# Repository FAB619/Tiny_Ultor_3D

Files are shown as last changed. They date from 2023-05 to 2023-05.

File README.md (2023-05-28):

<div align="center"><h1 style=align="center">Tiny ULTOR</h1></div>

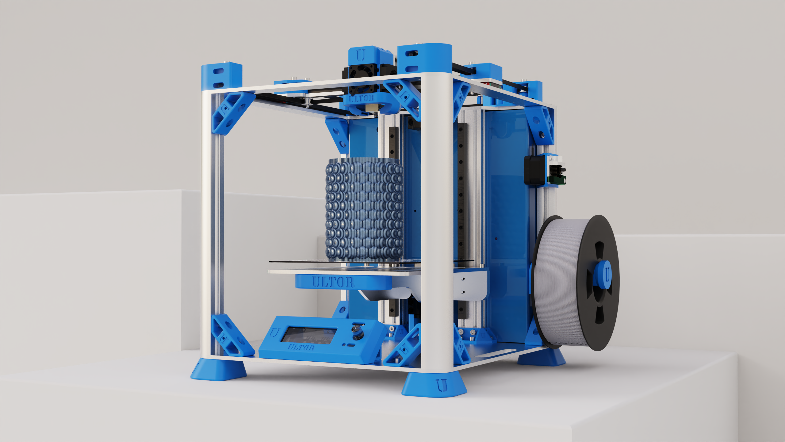
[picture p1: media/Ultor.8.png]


Introduction 
--
Welcome to the **TINY ULTOR** machine documentation.

**We are excited to share our open-source 3D printer project in collaboration with Inmachines Gmbh!!**

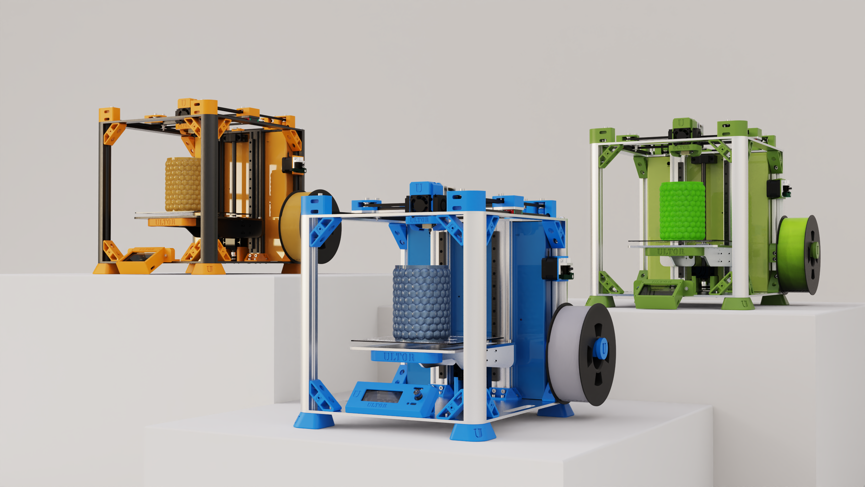
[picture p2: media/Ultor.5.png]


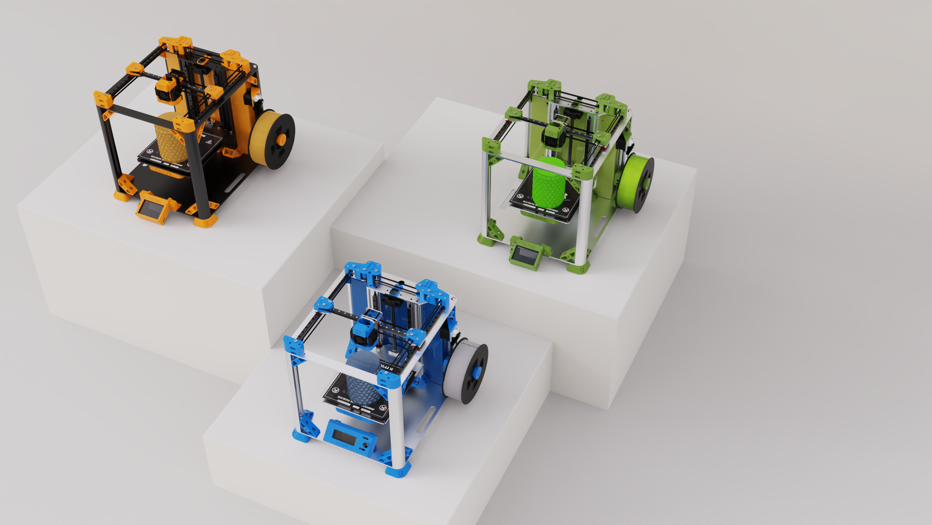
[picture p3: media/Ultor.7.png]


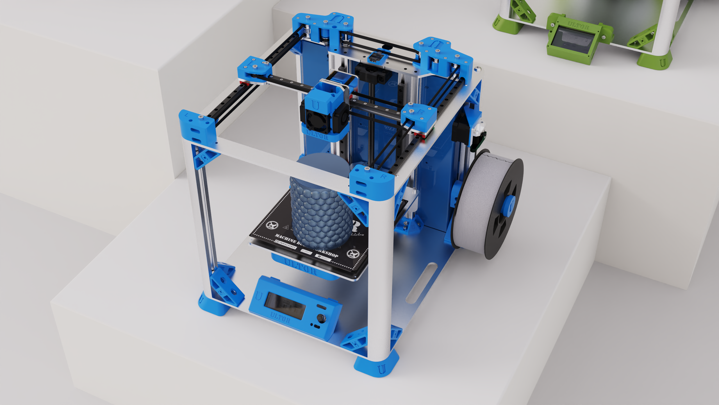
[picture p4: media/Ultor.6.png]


Specifications
--
- Build volume: 200x200x200mm
- Sturdy aluminium frame for stability and reduced vibration
- bed: aluminum with  non-sticking layer
- motion: COREXY system with GT2 6mm belt, Z axis: Sfu 1204 Ballscrew.
- guides: 9 & 12mm linear shaft, Hiwin MGN Series 9 & 12mm linear rails. MGN9 for XY axis an MGN12 for Z axis.
- motors: stepper motor NEMA 17
- drivers: trinamic TMC2208
- adjustable and heated printing bed
- Screens: Touchscreen HMI interface for easy operation / Reprap LCD 2004
- Pcb Board: **[Rumba3D-SPLink](https://github.com/FAB619/Rumba3D-SPLink)** board.

Electronics
----

Electronics design are one of the key features of FAB619 products. All products are 100% designed & made in tunisia. The electronics and boards are designed locally and fully functional with more addons.



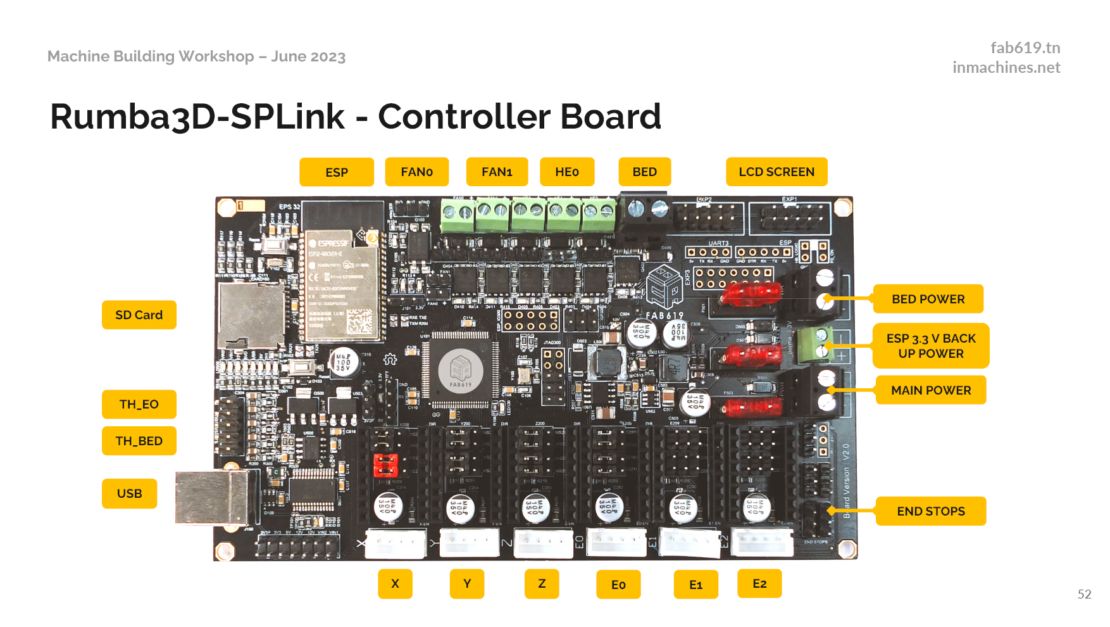
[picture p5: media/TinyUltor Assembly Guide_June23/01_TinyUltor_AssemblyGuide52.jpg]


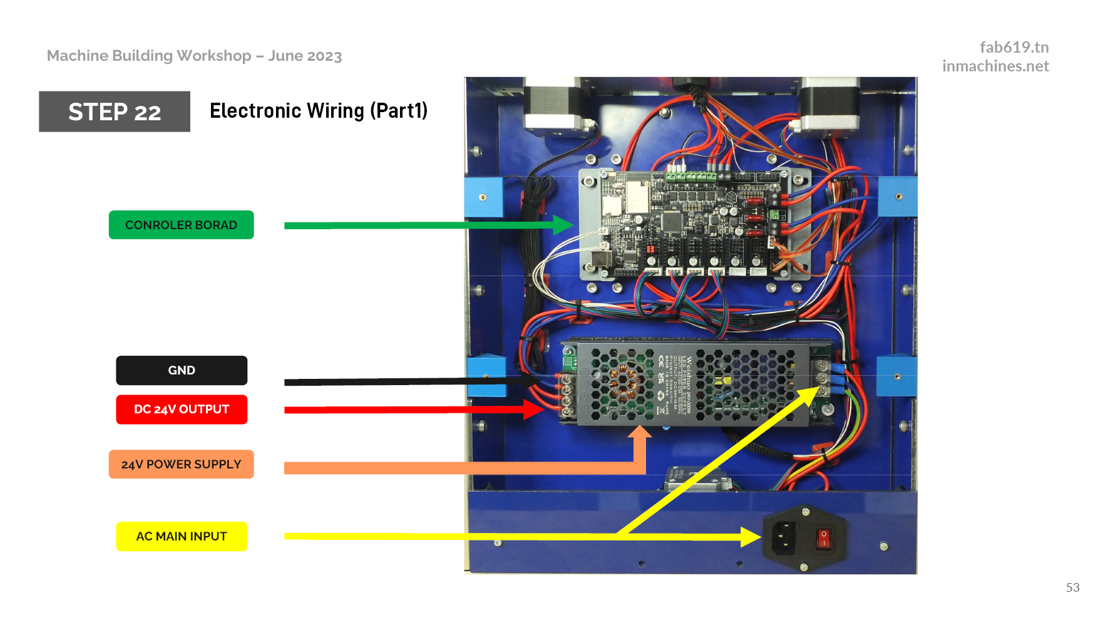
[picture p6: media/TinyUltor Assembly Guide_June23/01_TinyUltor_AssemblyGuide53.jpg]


Files 
--
 - **[CAD Files](https://github.com/FAB619/Tiny_Ultor_3D/tree/main/CAD)**
 - **[Fabrication Files](https://github.com/FAB619/Tiny_Ultor_3D/tree/main/Fabrication)**
- **[Assembly Book](https://github.com/FAB619/Tiny_Ultor_3D/wiki/Tiny-Ultor-3D-Assembly-Guide)**
- **[Firmware ](https://github.com/FAB619/Tiny_Ultor_3D/tree/main/Firmware/Marlin-2.0.9.6)**

3D printing Test 
--
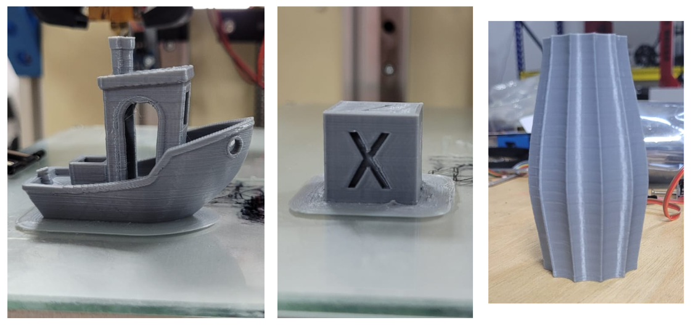
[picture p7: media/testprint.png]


Acknowledgements
--
The development of this machine is part of **Digital4Job Project** implemented by: 
* **[Helmut-Schmidt-Universität Universität der Bundeswehr](https://www.hsu-hh.de/en/)** Laboratorium Fertigungstechnik Holstenhofweg 85 22043 Hamburg
* **[OpenLab Hamburg](https://openlab-hamburg.de/startpage/)**
* **[GIZ](https://www.giz.de/en/worldwide/326.html)**

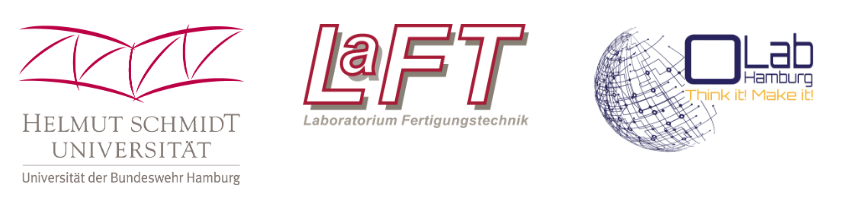
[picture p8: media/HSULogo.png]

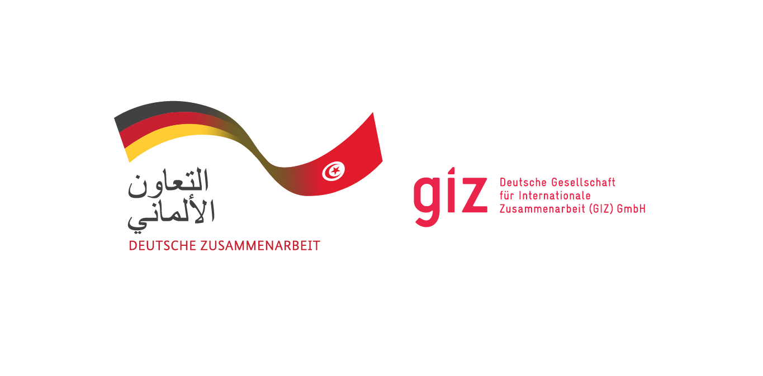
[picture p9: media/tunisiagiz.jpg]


In partnership with: 
* **[InMachines Ingrassia GmbH](https://www.inmachines.net/)**

* **[Fab619 On-Demand-Fabrication](https://fab619.tn/)**



License
--

Hardware design, CAD and PCB files, BOM, settings and other technical or design files are released under the following license:

- CERN Open Hardware Licence Version 2 Weakly Reciprocal - **[CERN-OHL-W](LICENSE_CERN_OHL_W_V2.txt)**

Assembly manual, pictures, videos, presentations, description text and other type of media are released under the following license:

- Creative-Commons-Attribution-ShareAlike 4.0 International - **[CC BY-SA 4.0](LICENSE_CC_BY_SA_4.0.txt)**

**License Owner **[InMachines Ingrassia GmbH](https://www.inmachines.net/)****

Author
--

**Tiny ULTOR** 3D Printer has been designed and built by **[Fab619 On-Demand-Fabrication](https://fab619.tn/)** & **[InMachines Ingrassia GmbH](https://www.inmachines.net/)**.



<br>

<b>FAB619 Design Team:</b>

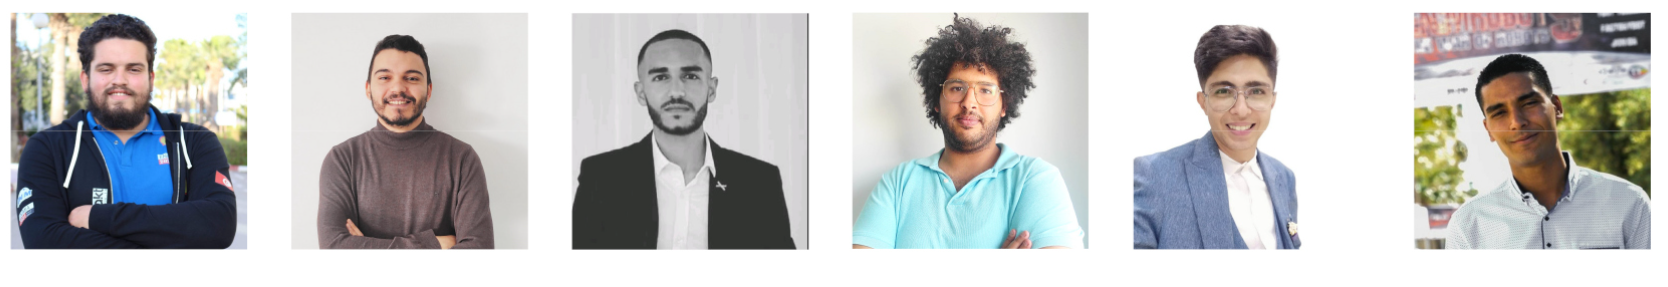
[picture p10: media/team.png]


<b> [Kais ALILA](http://fabacademy.org/2020/labs/kamplintfort/students/kais-alila/) | [Mhamed ALILA](https://www.behance.net/alilamhamed) | [Zomita Khayreddine](https://www.linkedin.com/in/zomita-khayreddine-916718217/) | [Ltifi Haythem](https://www.linkedin.com/in/haythemltifi/) | [Samer Jawadi](https://www.linkedin.com/in/samer-jawadi/) | [Ahmed Kaddour Belaid](https://www.linkedin.com/in/ahmed-kaddour-belaid-a6854418a/) </b>

Note
--
This documentation will be continuously improved as soon there are updates and/or improvements on the machine.

Disclaimer
--

This hardware/software is provided "as is", and you use the hardware/software at your own risk. Under no circumstances shall any author be liable for direct, indirect, special, incidental, or consequential damages resulting from the use, misuse, or inability to use this hardware/software, even if the authors have been advised of the possibility of such damages.

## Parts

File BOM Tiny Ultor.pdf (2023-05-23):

Category | ID | Item | Qte
| 1 | Nema 17 17HS4401 0.49NM | 4
| 2 | TMC2208 - Stepper Driver | 4
| 3 | Extruder Head CR8 1.75mm Nozzle 0.4mm 24V | 1
| 4 | Heat Bed MK2B | 1
| 5 | AC PSU Cable | 1
| 6 | PSU 24V 12,5A 300W | 1
| 7 | PCB Board Rumba Plus FAB619 | 1
| 8 | Turbo Cooling FAN 24V 40x40x10mm | 1
| 9 | Cooling FAN 12V 40x40x10mm | 1
| 10 | PI Zero WH | 1
| 11 | TFT screen RPI 3,5inch | 1
| 12 | LCD 2004 Reprap Screen | 1
| 13 | HDMI Cable | 1
| 14 | USB Tyope B cable | 1
| 15
| 16
| 17 | 2GT-20-6 T 5M Pulley Z=20 | 2
| 18 | 2GT-6 T=5mm Idler pulley 6mm | 14
| 19 | MGN9 300MM + MGN9H | 1
| 20 | MGN9 350MM + MGN9H | 2
| 21 | MGN2 300MM + MGN12H | 2
| 22 | Brass Spacer M3*30*6MM | 4
| 23 | Brass Spacer M3*10*6MM | 4
| 24 | SFU1204-300MM BallScrew | 1
| 25 | BK10 bearing | 1
| 26 | BF10 Bearing | 1
| 27 | MK8 Extruder 1.75MM right | 1
| 28 | 2GT-20-6 T=8MM Pulley Z= 60 | 1
| 29 | 2GT-60-6 T=5MM Pulley Z= 60 for 6MM Tinming belt | 1
| 30 | Aluminium Extrusion Rounded 30x30 R8 L2000MM | 1
| 31 | Machine Footer D=40mm M8 | 4
| 32

### Mecanichal Parts

### Electronics

Raw Material | 33
| 34 | PLA 1,75 1kg | 2
| 35 | Plexiglass Acrilyc 4mm Transparen 500x500mm | 1
| 36 | Aluminium Composites 3mm Blue 500x500mm | 1
| 37
| 38 | DIN912 M3x8 | 150
| 39 | DIN912 M3x12 | 28
| 40 | DIN912 M3x14 | 4
| 41 | DIN912 M3x16 | 23
| 42 | DIN912 M3x25 | 4
| 43 | DIN912 M3x30 | 4
| 44 | DIN912 M4x10 | 10
| 45 | DIN912 M5x10 | 62
| 46 | DIN912 M5x16 | 6
| 47 | DIN912 M5x25 | 4
| 48 | DIN912 M5x30 | 2
| 49 | DIN912 M5x40 | 13
| 50 | ISO7380 M6x10 | 8
| 51 | ISO7380 M8x16 | 4
| 52 | T-Nut M3 R6 2020 | 24
| 53 | T-Nut M5 R8 3030 | 26
| 54 | T-Nut M5 R6 2020 | 16
| 55 | T-Nut M4 R8 3030 | 2
| 56 | M3 Nut | 16
| 57 | M5 Nut | 2

### Fastners

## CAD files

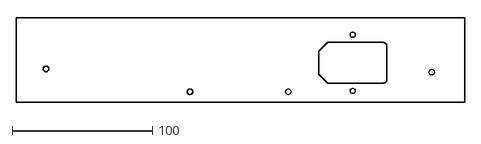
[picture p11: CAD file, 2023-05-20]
Fabrication/Milling & cutting/Aluminium Composites/PSU Connector back Pannel.dxf
320.0 x 60.0

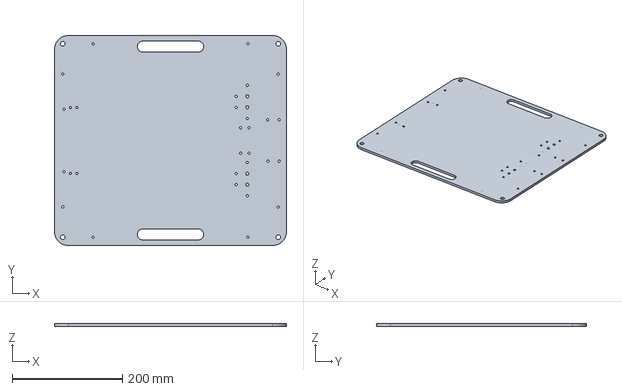
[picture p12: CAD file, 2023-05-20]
Fabrication/Milling & cutting/Metal Parts/D005 v3.stp
420.0 x 380.0 x 5.00 mm

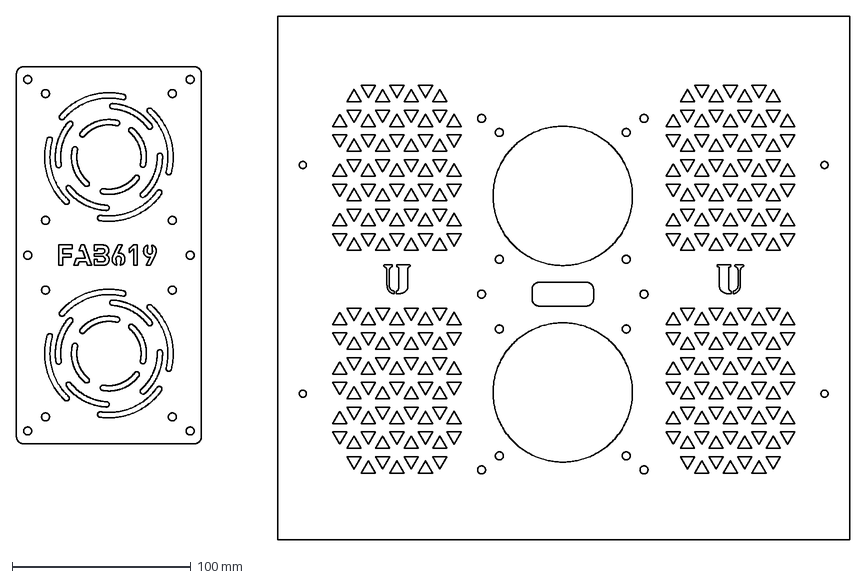
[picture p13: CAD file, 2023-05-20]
Fabrication/Milling & cutting/Plexiglass 4mm Laser Cut/Elec panel_plexi 4mm.dxf
466.3 x 293.1 mm

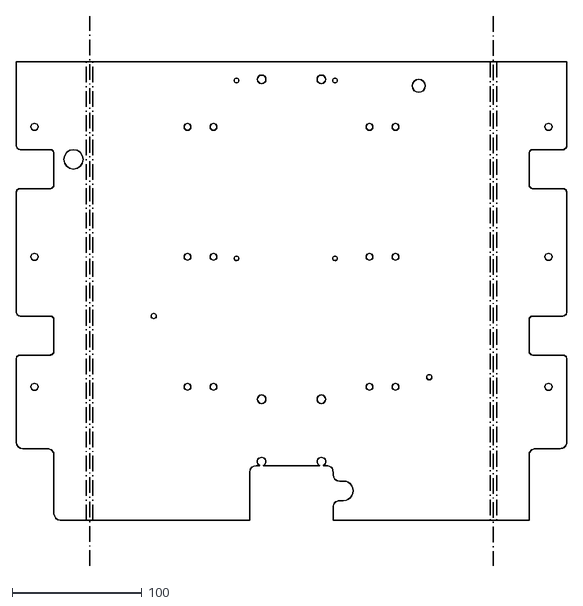
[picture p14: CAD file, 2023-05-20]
Fabrication/Milling & cutting/Aluminium Composites/elec Pannel.dxf
423.4 x 423.0

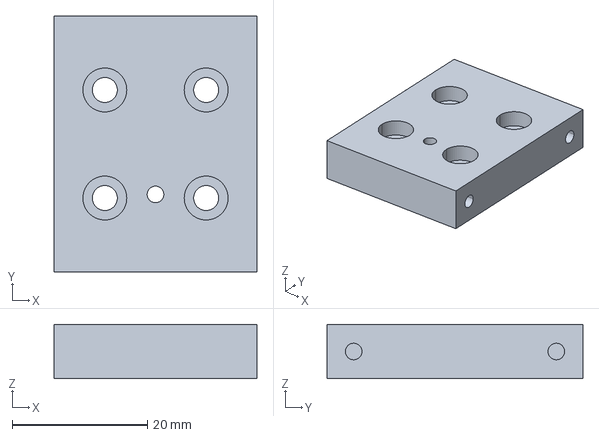
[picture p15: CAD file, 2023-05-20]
Fabrication/Milling & cutting/Metal Parts/D006.stp
30.0 x 37.9 x 8.00 mm

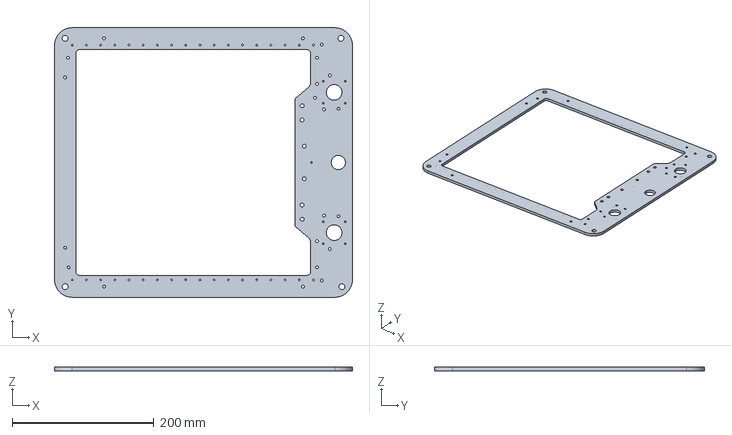
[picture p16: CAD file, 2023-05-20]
Fabrication/Milling & cutting/Metal Parts/D001 V3.stp
420.0 x 380.0 x 5.00 mm

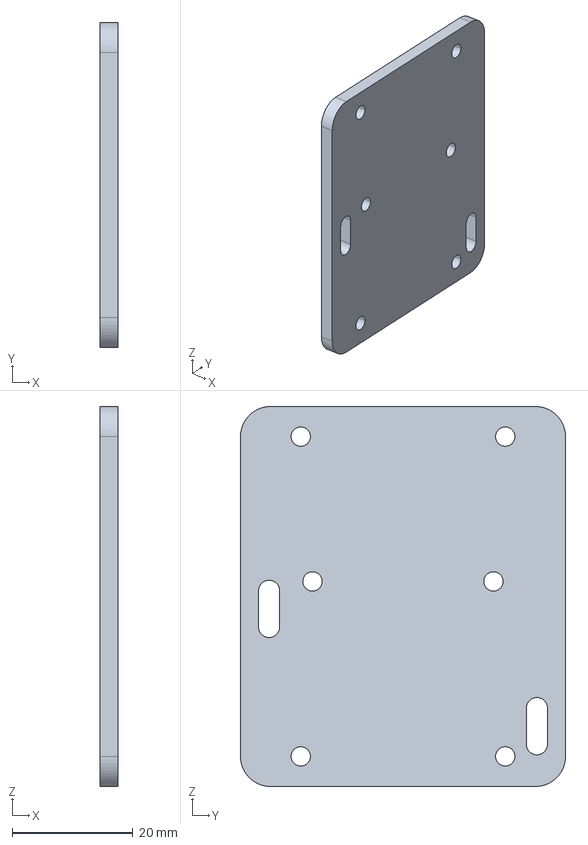
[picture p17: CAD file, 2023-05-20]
Fabrication/Milling & cutting/Metal Parts/D008.stp
3.00 x 53.9 x 63.0 mm

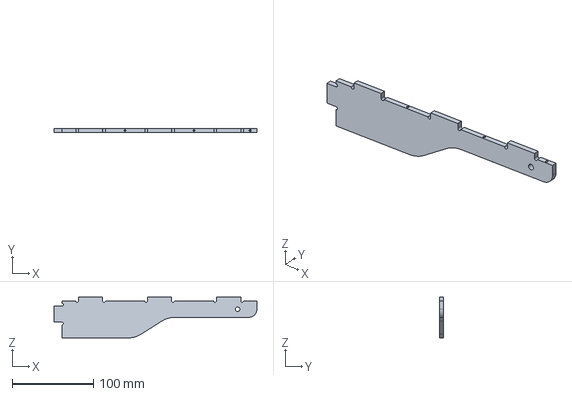
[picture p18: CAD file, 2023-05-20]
Fabrication/Milling & cutting/Metal Parts/D003.stp
250.0 x 5.00 x 50.4 mm

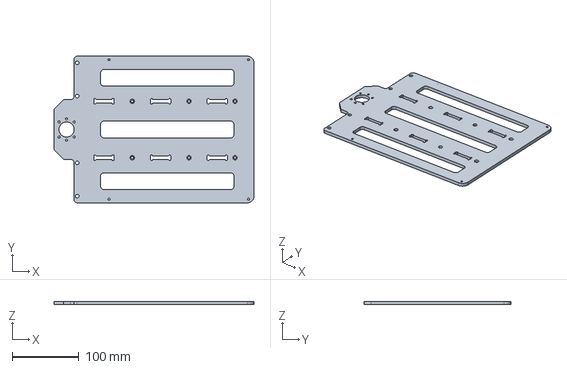
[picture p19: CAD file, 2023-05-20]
Fabrication/Milling & cutting/Metal Parts/D002.stp
299.9 x 220.0 x 5.00 mm

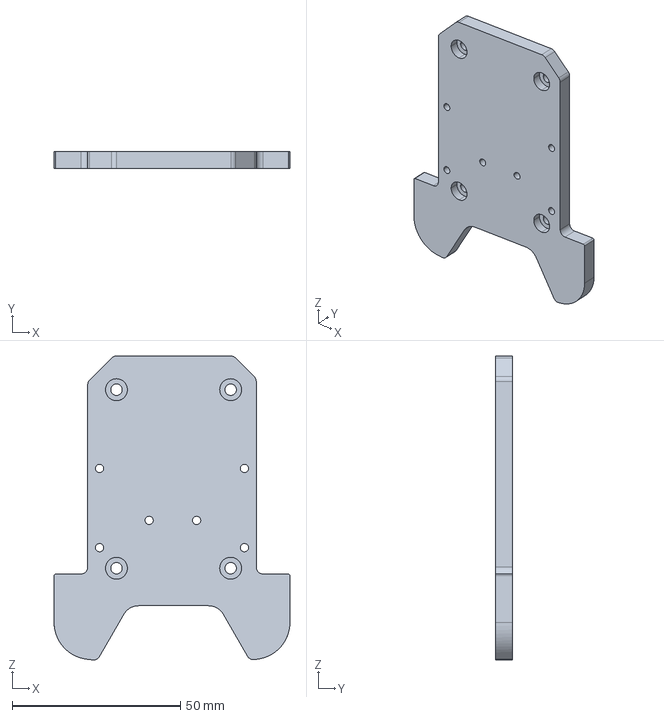
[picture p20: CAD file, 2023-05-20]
Fabrication/Milling & cutting/Metal Parts/D009.stp
70.0 x 5.00 x 90.2 mm

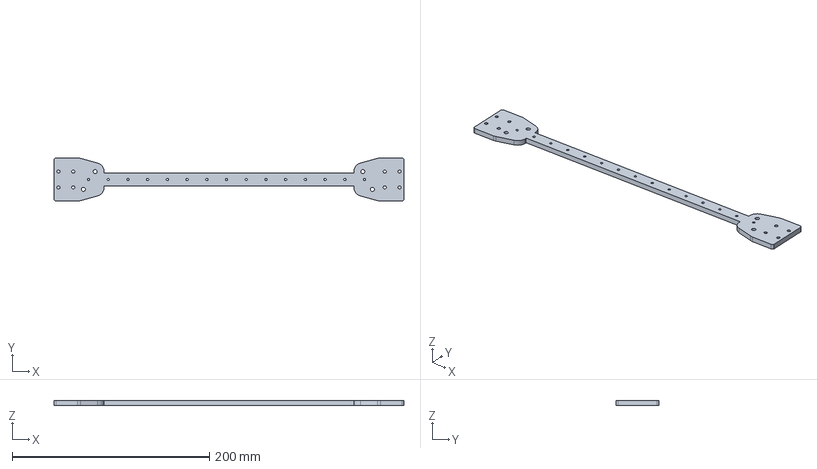
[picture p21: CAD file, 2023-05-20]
Fabrication/Milling & cutting/Metal Parts/D010.stp
355.0 x 43.9 x 5.00 mm

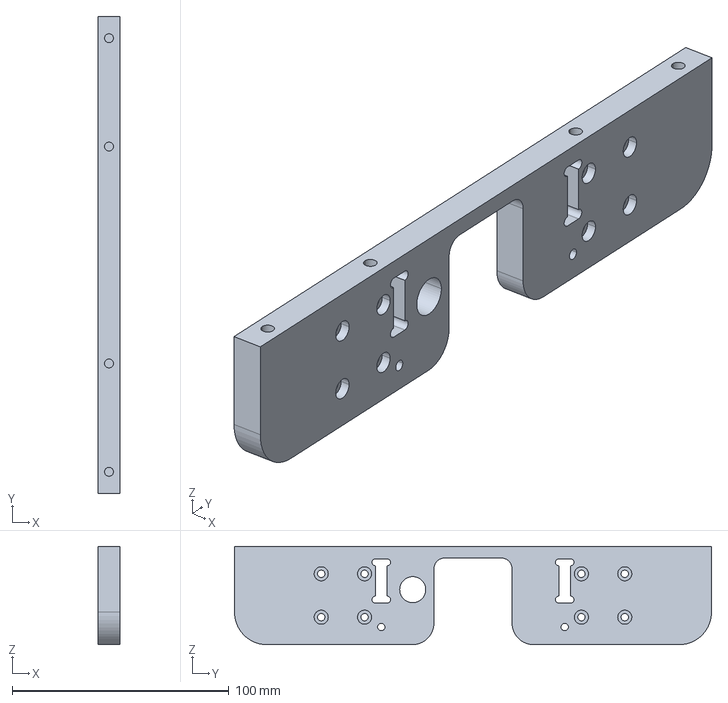
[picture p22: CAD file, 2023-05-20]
Fabrication/Milling & cutting/Metal Parts/D004.stp
10.0 x 220.0 x 45.4 mm

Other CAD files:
Fabrication/Milling & cutting/Metal Parts/D007.stp

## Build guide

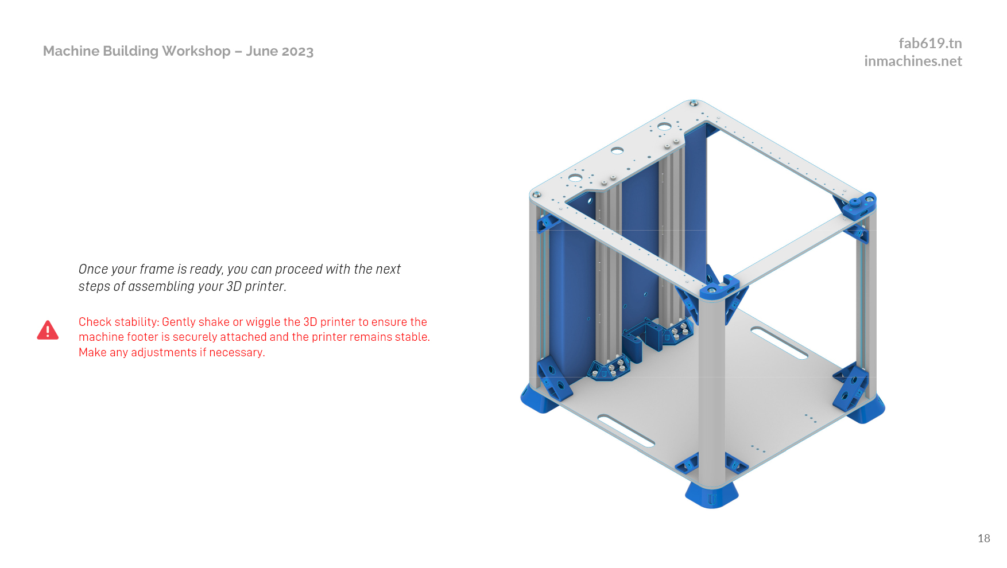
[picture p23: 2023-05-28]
media/TinyUltor Assembly Guide_June23/01_TinyUltor_AssemblyGuide18.jpg

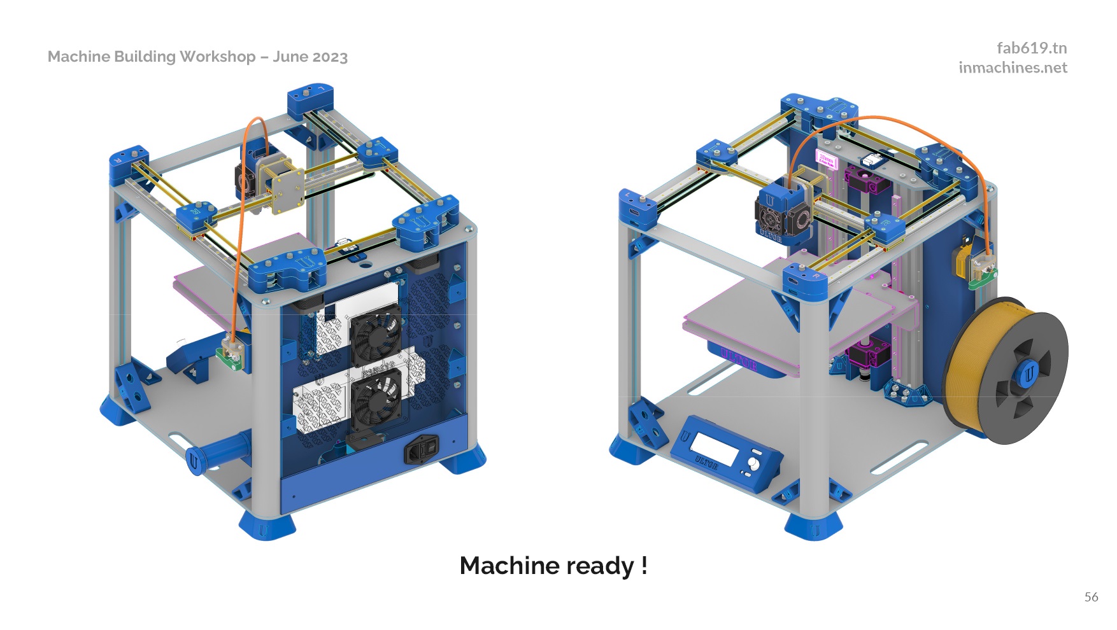
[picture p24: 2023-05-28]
media/TinyUltor Assembly Guide_June23/01_TinyUltor_AssemblyGuide56.jpg

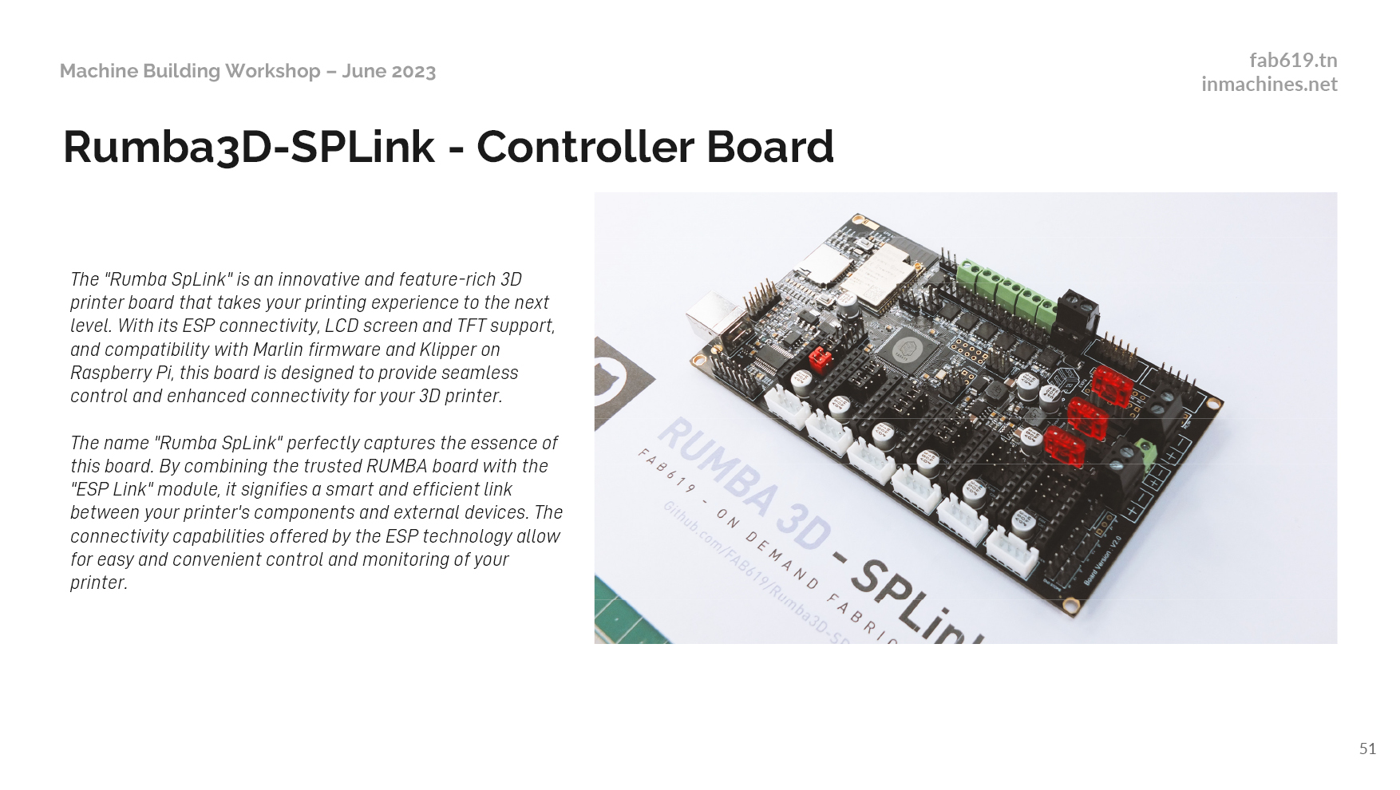
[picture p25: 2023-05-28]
media/TinyUltor Assembly Guide_June23/01_TinyUltor_AssemblyGuide51.jpg

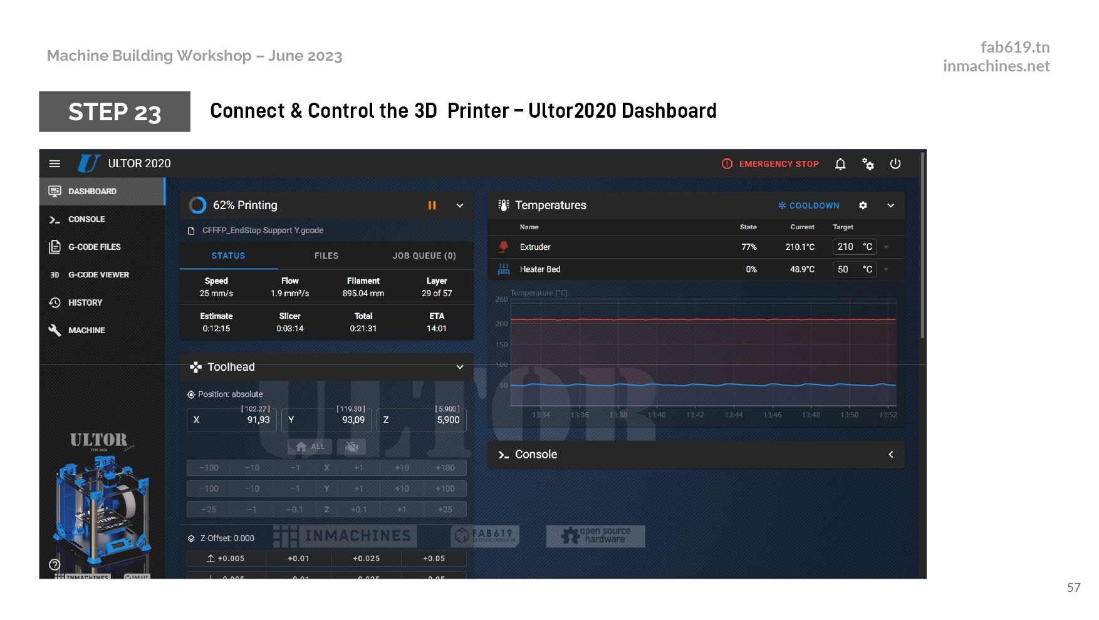
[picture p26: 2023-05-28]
media/TinyUltor Assembly Guide_June23/01_TinyUltor_AssemblyGuide57.jpg

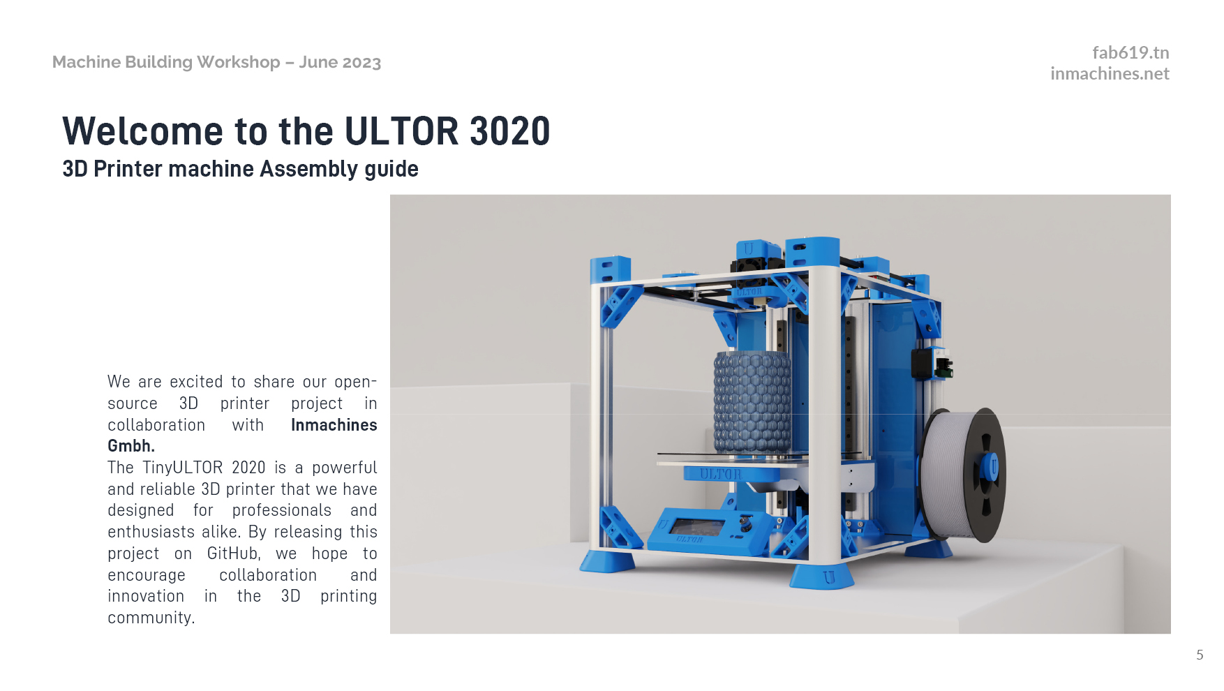
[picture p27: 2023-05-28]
media/TinyUltor Assembly Guide_June23/01_TinyUltor_AssemblyGuide5.jpg

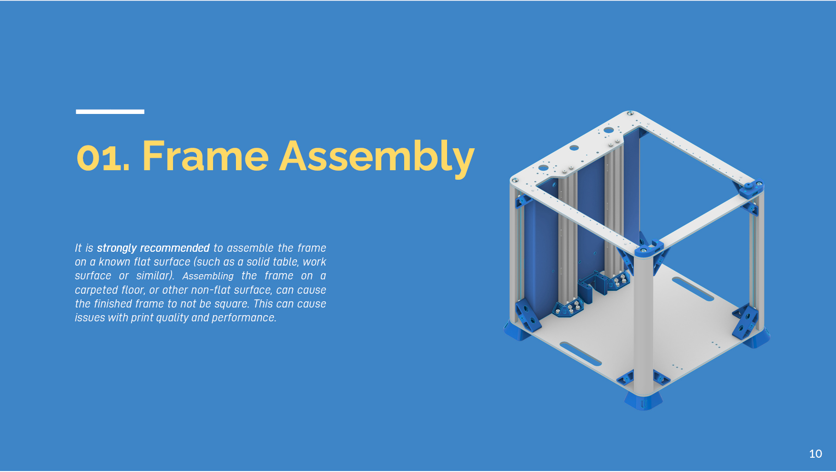
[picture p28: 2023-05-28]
media/TinyUltor Assembly Guide_June23/01_TinyUltor_AssemblyGuide10.jpg

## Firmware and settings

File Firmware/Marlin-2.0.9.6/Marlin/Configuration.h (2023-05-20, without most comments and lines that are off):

#pragma once
#define CONFIGURATION_H_VERSION 02000905
#define STRING_CONFIG_H_AUTHOR "(none, default config)" // Who made the changes.
#define SHOW_BOOTSCREEN
  #define MOTHERBOARD BOARD_RUMBA
#define SERIAL_PORT 0
#define BAUDRATE 250000
#define X_DRIVER_TYPE  A4988
#define Y_DRIVER_TYPE  A4988
#define Z_DRIVER_TYPE  A4988
#define E0_DRIVER_TYPE A4988
#define EXTRUDERS 1
#define DEFAULT_NOMINAL_FILAMENT_DIA 1.75
#define TEMP_SENSOR_0 1
#define TEMP_SENSOR_1 0
#define TEMP_SENSOR_2 0
#define TEMP_SENSOR_3 0
#define TEMP_SENSOR_4 0
#define TEMP_SENSOR_5 0
#define TEMP_SENSOR_6 0
#define TEMP_SENSOR_7 0
#define TEMP_SENSOR_BED 1
#define TEMP_SENSOR_PROBE 0
#define TEMP_SENSOR_CHAMBER 0
#define TEMP_SENSOR_COOLER 0
#define TEMP_SENSOR_BOARD 0
#define TEMP_SENSOR_REDUNDANT 0
#define DUMMY_THERMISTOR_998_VALUE  25
#define DUMMY_THERMISTOR_999_VALUE 100
#define TEMP_RESIDENCY_TIME         10  // (seconds) Time to wait for hotend to "settle" in M109
#define TEMP_WINDOW                  1  // (°C) Temperature proximity for the "temperature reached" timer
#define TEMP_HYSTERESIS              3  // (°C) Temperature proximity considered "close enough" to the target
#define TEMP_BED_RESIDENCY_TIME     10  // (seconds) Time to wait for bed to "settle" in M190
#define TEMP_BED_WINDOW              1  // (°C) Temperature proximity for the "temperature reached" timer
#define TEMP_BED_HYSTERESIS          3  // (°C) Temperature proximity considered "close enough" to the target
#define TEMP_CHAMBER_RESIDENCY_TIME 10  // (seconds) Time to wait for chamber to "settle" in M191
#define TEMP_CHAMBER_WINDOW          1  // (°C) Temperature proximity for the "temperature reached" timer
#define TEMP_CHAMBER_HYSTERESIS      3  // (°C) Temperature proximity considered "close enough" to the target
#if TEMP_SENSOR_REDUNDANT
  #define TEMP_SENSOR_REDUNDANT_SOURCE    E1  // The sensor that will provide the redundant reading.
  #define TEMP_SENSOR_REDUNDANT_TARGET    E0  // The sensor that we are providing a redundant reading for.
  #define TEMP_SENSOR_REDUNDANT_MAX_DIFF  10  // (°C) Temperature difference that will trigger a print abort.
#endif
#define HEATER_0_MINTEMP   5
#define HEATER_1_MINTEMP   5
#define HEATER_2_MINTEMP   5
#define HEATER_3_MINTEMP   5
#define HEATER_4_MINTEMP   5
#define HEATER_5_MINTEMP   5
#define HEATER_6_MINTEMP   5
#define HEATER_7_MINTEMP   5
#define BED_MINTEMP        5
#define CHAMBER_MINTEMP    5
#define HEATER_0_MAXTEMP 275
#define HEATER_1_MAXTEMP 275
#define HEATER_2_MAXTEMP 275
#define HEATER_3_MAXTEMP 275
#define HEATER_4_MAXTEMP 275
#define HEATER_5_MAXTEMP 275
#define HEATER_6_MAXTEMP 275
#define HEATER_7_MAXTEMP 275
#define BED_MAXTEMP      150
#define CHAMBER_MAXTEMP  60
#define HOTEND_OVERSHOOT 15   // (°C) Forbid temperatures over MAXTEMP - OVERSHOOT
#define BED_OVERSHOOT    10   // (°C) Forbid temperatures over MAXTEMP - OVERSHOOT
#define COOLER_OVERSHOOT  2   // (°C) Forbid temperatures closer than OVERSHOOT
#define PIDTEMP          // See the PID Tuning Guide at https://reprap.org/wiki/PID_Tuning
#define BANG_MAX 255     // Limits current to nozzle while in bang-bang mode; 255=full current
#define PID_MAX BANG_MAX // Limits current to nozzle while PID is active (see PID_FUNCTIONAL_RANGE below); 255=full current
#define PID_K1 0.95      // Smoothing factor within any PID loop
    #define DEFAULT_Kp  22.2
    #define DEFAULT_Ki   1.08
    #define DEFAULT_Kd 114.00
#define MAX_BED_POWER 255 // limits duty cycle to bed; 255=full current
#define MAX_CHAMBER_POWER 255 // limits duty cycle to chamber heater; 255=full current
  #define PID_FUNCTIONAL_RANGE 10 // If the temperature difference between the target temperature and the actual temperature
#define PREVENT_COLD_EXTRUSION
#define EXTRUDE_MINTEMP 20
#define PREVENT_LENGTHY_EXTRUDE
#define EXTRUDE_MAXLENGTH 200
#define THERMAL_PROTECTION_HOTENDS // Enable thermal protection for all extruders
#define THERMAL_PROTECTION_BED     // Enable thermal protection for the heated bed
#define THERMAL_PROTECTION_CHAMBER // Enable thermal protection for the heated chamber
#define THERMAL_PROTECTION_COOLER  // Enable thermal protection for the laser cooling
#define COREXY
#define USE_XMIN_PLUG
#define USE_ZMIN_PLUG
#define USE_YMAX_PLUG
#define ENDSTOPPULLUPS
#define X_MIN_ENDSTOP_INVERTING true // Set to true to invert the logic of the endstop.
#define Y_MIN_ENDSTOP_INVERTING true // Set to true to invert the logic of the endstop.
#define Z_MIN_ENDSTOP_INVERTING true // Set to true to invert the logic of the endstop.
#define I_MIN_ENDSTOP_INVERTING false // Set to true to invert the logic of the endstop.
#define J_MIN_ENDSTOP_INVERTING false // Set to true to invert the logic of the endstop.
#define K_MIN_ENDSTOP_INVERTING false // Set to true to invert the logic of the endstop.
#define X_MAX_ENDSTOP_INVERTING false // Set to true to invert the logic of the endstop.
#define Y_MAX_ENDSTOP_INVERTING true // Set to true to invert the logic of the endstop.
#define Z_MAX_ENDSTOP_INVERTING false // Set to true to invert the logic of the endstop.
#define I_MAX_ENDSTOP_INVERTING false // Set to true to invert the logic of the endstop.
#define J_MAX_ENDSTOP_INVERTING false // Set to true to invert the logic of the endstop.
#define K_MAX_ENDSTOP_INVERTING false // Set to true to invert the logic of the endstop.
#define Z_MIN_PROBE_ENDSTOP_INVERTING false // Set to true to invert the logic of the probe.
#define DEFAULT_AXIS_STEPS_PER_UNIT   { 80, 80, 266.67, 100 }
#define DEFAULT_MAX_FEEDRATE          { 300, 300, 25, 25 }
#define DEFAULT_MAX_ACCELERATION      { 500, 500, 100, 10000 }
#define DEFAULT_ACCELERATION          500    // X, Y, Z ... and E acceleration for printing moves
#define DEFAULT_RETRACT_ACCELERATION  500    // E acceleration for retracts
#define DEFAULT_TRAVEL_ACCELERATION   3000    // X, Y, Z ... acceleration for travel (non printing) moves
#define DEFAULT_EJERK    5.0  // May be used by Linear Advance
  #define JUNCTION_DEVIATION_MM 0.013 // (mm) Distance from real junction edge
  #define JD_HANDLE_SMALL_SEGMENTS    // Use curvature estimation instead of just the junction angle
#define Z_MIN_PROBE_USES_Z_MIN_ENDSTOP_PIN
#define NOZZLE_TO_PROBE_OFFSET { 10, 10, 0 }
#define PROBING_MARGIN 10
#define XY_PROBE_FEEDRATE (133*60)
#define Z_PROBE_FEEDRATE_FAST (4*60)
#define Z_PROBE_FEEDRATE_SLOW (Z_PROBE_FEEDRATE_FAST / 2)
#define Z_CLEARANCE_DEPLOY_PROBE   10 // Z Clearance for Deploy/Stow
#define Z_CLEARANCE_BETWEEN_PROBES  5 // Z Clearance between probe points
#define Z_CLEARANCE_MULTI_PROBE     5 // Z Clearance between multiple probes
#define Z_PROBE_LOW_POINT          -2 // Farthest distance below the trigger-point to go before stopping
#define Z_PROBE_OFFSET_RANGE_MIN -20
#define Z_PROBE_OFFSET_RANGE_MAX 20
#define X_ENABLE_ON 0
#define Y_ENABLE_ON 0
#define Z_ENABLE_ON 0
#define E_ENABLE_ON 0 // For all extruders
#define DISABLE_X false
#define DISABLE_Y false
#define DISABLE_Z false
#define DISABLE_E false             // Disable the extruder when not stepping
#define DISABLE_INACTIVE_EXTRUDER   // Keep only the active extruder enabled
#define INVERT_X_DIR false
#define INVERT_Y_DIR true
#define INVERT_Z_DIR false
#define INVERT_E0_DIR true
#define INVERT_E1_DIR false
#define INVERT_E2_DIR false
#define INVERT_E3_DIR false
#define INVERT_E4_DIR false
#define INVERT_E5_DIR false
#define INVERT_E6_DIR false
#define INVERT_E7_DIR false
#define X_HOME_DIR -1
#define Y_HOME_DIR 1
#define Z_HOME_DIR -1
#define X_BED_SIZE 200
#define Y_BED_SIZE 200
#define X_MIN_POS 0
#define Y_MIN_POS 0
#define Z_MIN_POS 0
#define X_MAX_POS X_BED_SIZE
#define Y_MAX_POS Y_BED_SIZE
#define Z_MAX_POS 200
#define MIN_SOFTWARE_ENDSTOPS
  #define MIN_SOFTWARE_ENDSTOP_X
  #define MIN_SOFTWARE_ENDSTOP_Y
  #define MIN_SOFTWARE_ENDSTOP_Z
  #define MIN_SOFTWARE_ENDSTOP_I
  #define MIN_SOFTWARE_ENDSTOP_J
  #define MIN_SOFTWARE_ENDSTOP_K
#define MAX_SOFTWARE_ENDSTOPS
  #define MAX_SOFTWARE_ENDSTOP_X
  #define MAX_SOFTWARE_ENDSTOP_Y
  #define MAX_SOFTWARE_ENDSTOP_Z
  #define MAX_SOFTWARE_ENDSTOP_I
  #define MAX_SOFTWARE_ENDSTOP_J
  #define MAX_SOFTWARE_ENDSTOP_K
#define HOMING_FEEDRATE_MM_M { (50*60), (50*60), (4*60) }
#define VALIDATE_HOMING_ENDSTOPS
#define EEPROM_SETTINGS     // Persistent storage with M500 and M501
#define EEPROM_CHITCHAT       // Give feedback on EEPROM commands. Disable to save PROGMEM.
#define EEPROM_BOOT_SILENT    // Keep M503 quiet and only give errors during first load
#define HOST_KEEPALIVE_FEATURE        // Disable this if your host doesn't like keepalive messages
#define DEFAULT_KEEPALIVE_INTERVAL 2  // Number of seconds between "busy" messages. Set with M113.
#define BUSY_WHILE_HEATING            // Some hosts require "busy" messages even during heating
#define PREHEAT_1_LABEL       "PLA"
#define PREHEAT_1_TEMP_HOTEND 200
#define PREHEAT_1_TEMP_BED     50
#define PREHEAT_1_TEMP_CHAMBER 35
#define PREHEAT_1_FAN_SPEED     0 // Value from 0 to 255
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

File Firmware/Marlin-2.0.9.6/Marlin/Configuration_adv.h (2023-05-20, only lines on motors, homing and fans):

#define E0_AUTO_FAN_PIN 8
#define E1_AUTO_FAN_PIN -1
#define E2_AUTO_FAN_PIN -1
#define E3_AUTO_FAN_PIN -1
#define E4_AUTO_FAN_PIN -1
#define E5_AUTO_FAN_PIN -1
#define E6_AUTO_FAN_PIN -1
#define E7_AUTO_FAN_PIN -1
#define CHAMBER_AUTO_FAN_PIN -1
#define COOLER_AUTO_FAN_PIN 6
#define HOMING_BUMP_MM      { 5, 5, 2 }       // (mm) Backoff from endstops after first bump
#define HOMING_BUMP_DIVISOR { 2, 2, 4 }       // Re-Bump Speed Divisor (Divides the Homing Feedrate)
#define MICROSTEP_MODES { 16, 16, 16, 16, 16, 16 } // [1,2,4,8,16]

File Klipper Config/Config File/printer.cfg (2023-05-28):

# This file contains common pin mappings for RUMBA boards.  To use
# this config, the firmware should be compiled for the AVR atmega2560.

# See docs/Config_Reference.md for a description of parameters.

[stepper_x]
step_pin: PH0
dir_pin: !PH1
enable_pin: !PL1
microsteps: 16
rotation_distance: 40
endstop_pin: ^!PC0
#endstop_pin: ^PC1
position_endstop: 0
position_max: 200
homing_speed: 50

[stepper_y]
step_pin: PF0
dir_pin: !PL2
enable_pin: !PF1
microsteps: 16
rotation_distance: 40
#endstop_pin: ^!PC2
endstop_pin: ^!PC3
position_endstop: 200
position_max: 204
homing_speed: 50
homing_positive_dir: true

[stepper_z]
step_pin: PF3
dir_pin: PF2
enable_pin: !PK0
microsteps: 16
rotation_distance: 12
endstop_pin: ^!PC4
#endstop_pin: ^PC5
position_endstop: 0.5
position_max: 200
homing_speed: 5
homing_retract_speed: 2
homing_retract_dist: 5.0


[extruder]
step_pin: PA1
dir_pin: !PA0
enable_pin: !PA2
microsteps: 16
rotation_distance: 34.4
nozzle_diameter: 0.400
filament_diameter: 1.750
heater_pin: PE4
sensor_type: EPCOS 100K B57560G104F
sensor_pin: PK7
control: pid
pid_Kp: 22.2
pid_Ki: 1.08
pid_Kd: 114
min_temp: 0
max_temp: 250

#[extruder1]
#step_pin: PA4
#dir_pin: PA3
#enable_pin: !PA5
#heater_pin: PE5
#sensor_pin: PK6
#...

#[extruder2]
#step_pin: PA7
#dir_pin: PA6
#enable_pin: !PG2
#heater_pin: PH3
#sensor_pin: PK5
#...

[heater_bed]
heater_pin: PH6
sensor_type: Generic 3950
sensor_pin: PK3
control: watermark
min_temp: 0
max_temp: 130

[fan]
pin: PH4

[heater_fan fan1]
pin: PH5
heater_temp: 50
fan_speed: 0.3

[mcu]
serial: /dev/serial/by-id/usb-FTDI_FT232R_USB_UART_A10N2OQF-if00-port0


[printer]
kinematics: corexy
max_velocity: 300
max_accel: 500
max_z_velocity: 50
max_z_accel: 100

[virtual_sdcard]
path: ~/printer_data/gcodes

[display_status]

[pause_resume]

[gcode_macro PAUSE]
description: Pause the actual running print
rename_existing: PAUSE_BASE
gcode:
  PAUSE_BASE
  _TOOLHEAD_PARK_PAUSE_CANCEL

[gcode_macro RESUME]
description: Resume the actual running print
rename_existing: RESUME_BASE
gcode:
  ##### read extrude from  _TOOLHEAD_PARK_PAUSE_CANCEL  macro #####
  {% set extrude = printer['gcode_macro _TOOLHEAD_PARK_PAUSE_CANCEL'].extrude %}
  #### get VELOCITY parameter if specified ####
  {% if 'VELOCITY' in params|upper %}
    {% set get_params = ('VELOCITY=' + params.VELOCITY)  %}
  {%else %}
    {% set get_params = "" %}
  {% endif %}
  ##### end of definitions #####
  {% if printer.extruder.can_extrude|lower == 'true' %}
    M83
    G1 E{extrude} F2100
    {% if printer.gcode_move.absolute_extrude |lower == 'true' %} M82 {% endif %}
  {% else %}
    {action_respond_info("Extruder not hot enough")}
  {% endif %}  
  RESUME_BASE {get_params}

[gcode_macro CANCEL_PRINT]
description: Cancel the actual running print
rename_existing: CANCEL_PRINT_BASE
variable_park: True
gcode:
  ## Move head and retract only if not already in the pause state and park set to true
  {% if printer.pause_resume.is_paused|lower == 'false' and park|lower == 'true'%}
    _TOOLHEAD_PARK_PAUSE_CANCEL
  {% endif %}
  TURN_OFF_HEATERS
  CANCEL_PRINT_BASE

[gcode_macro _TOOLHEAD_PARK_PAUSE_CANCEL]
description: Helper: park toolhead used in PAUSE and CANCEL_PRINT
variable_extrude: 1.0
gcode:
  ##### set park positon for x and y #####
  # default is your max posion from your printer.cfg
  {% set x_park = printer.toolhead.axis_maximum.x|float - 5.0 %}
  {% set y_park = printer.toolhead.axis_maximum.y|float - 5.0 %}
  {% set z_park_delta = 2.0 %}
  ##### calculate save lift position #####
  {% set max_z = printer.toolhead.axis_maximum.z|float %}
  {% set act_z = printer.toolhead.position.z|float %}
  {% if act_z < (max_z - z_park_delta) %}
    {% set z_safe = z_park_delta %}
  {% else %}
    {% set z_safe = max_z - act_z %}
  {% endif %}
  ##### end of definitions #####
  {% if printer.extruder.can_extrude|lower == 'true' %}
    M83
    G1 E-{extrude} F2100
    {% if printer.gcode_move.absolute_extrude |lower == 'true' %} M82 {% endif %}
  {% else %}
    {action_respond_info("Extruder not hot enough")}
  {% endif %}
  {% if "xyz" in printer.toolhead.homed_axes %}
    G91
    G1 Z{z_safe} F900
    G90
    G1 X{x_park} Y{y_park} F6000
    {% if printer.gcode_move.absolute_coordinates|lower == 'false' %} G91 {% endif %}
  {% else %}
    {action_respond_info("Printer not homed")}
  {% endif %}


# "RepRapDiscount 2004 Smart Controller" type displays
[display]
lcd_type: hd44780
rs_pin: PD2
e_pin: PL7
d4_pin: PD3
d5_pin: PD7
d6_pin: PG0
d7_pin: PG1
encoder_pins: ^PB5, ^PB6
click_pin: ^!PL6

# "RepRapDiscount 128x64 Full Graphic Smart Controller" type displays
#[display]
#lcd_type: st7920
#cs_pin: PD2
#sclk_pin: PD3
#sid_pin: PL7
#encoder_pins: ^PB5, ^PB6
#click_pin: ^!PL6

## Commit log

2023-05-20 milling step file upload
    [D001 V3.stp, D002.stp, D003.stp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]
2023-05-20 update miiling & cuting files
    [D001 V3.stp, D002.stp, D003.stp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]
2023-05-20 Update Firmware
    [Configuration.h, Configuration_adv.h, esp32.csv]
2023-05-23 Uoload BOM
2023-05-23 Upload CAD File
2023-05-28 upload Assembly Pic
2023-05-28 Klipper Hex
2023-05-28 Update klipper config
    [printer.cfg]

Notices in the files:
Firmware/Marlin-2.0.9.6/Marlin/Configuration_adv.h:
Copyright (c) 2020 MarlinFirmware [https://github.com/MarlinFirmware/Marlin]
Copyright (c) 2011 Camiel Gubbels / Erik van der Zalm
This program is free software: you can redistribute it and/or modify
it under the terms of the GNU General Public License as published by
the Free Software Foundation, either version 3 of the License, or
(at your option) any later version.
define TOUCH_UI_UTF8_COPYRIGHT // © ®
